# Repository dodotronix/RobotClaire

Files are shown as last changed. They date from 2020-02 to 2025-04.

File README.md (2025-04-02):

# ROBOT CLAIRE
This project is the result of three years of development from my high school
years. The main goal was to build my own robot from scratch, without using
common construction parts that are readily available in many hobbyist shops
today.

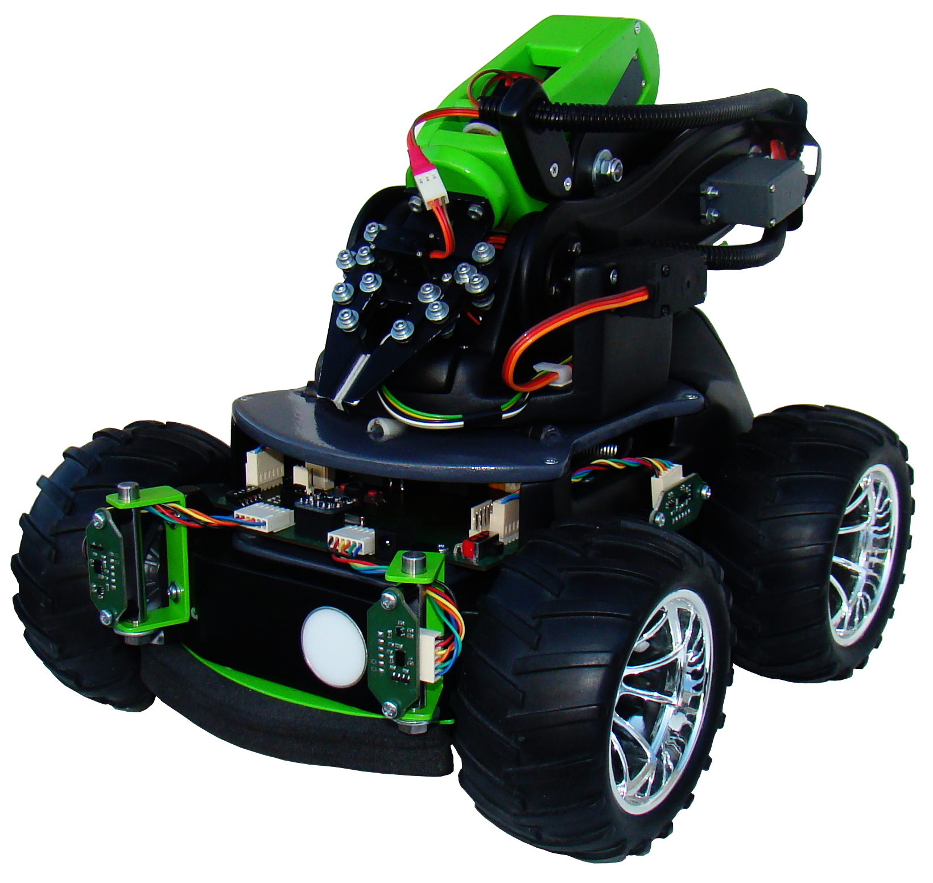
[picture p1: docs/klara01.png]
Robot

At the time when I was creating my robot, open-source CAD programs weren’t at a
sufficient level to design something that could be sent to a factory for
fabrication. For this reason, the mechanical design was created using Inventor
2013, while the electronic design was done using KiCad. The project has already
gone through three upgrades, but the first one wasn’t documented. However, I
did take some photos to capture the atmosphere of the very first steps in
development ([claire-rev0](https://drive.google.com/open?id=1PmOoYiifd_Xv0sS2DL9yxbEeKM7cLnv_)).

## NAVIGATION IN PROJECT
In the following folders, you will find README.md files with more detailed
descriptions of the content. Some folders also include additional information,
such as installation and execution instructions, particularly in directories
containing software. Please note that this repository is still under
development, and not all folders have been fully uploaded yet.

Video (http://www.youtube.com/watch?v=Z39dk2hXI14 "")

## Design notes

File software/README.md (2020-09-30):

# RASPBERRY PI application and diagram how it works

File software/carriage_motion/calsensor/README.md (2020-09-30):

# Calibration of IR triangulation sensors

## Analysis

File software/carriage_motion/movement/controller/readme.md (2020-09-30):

# PID controller design

## Analysis of input data
Data is read from the AddPU unit, which is sampling the number of ticks per
revolution of the motor shaft. Every motor has its ID (according to following
table) which is used to let the AddPU know, which data user want to read.

### Code identification
| Wheel | ID |
| :---: | :---: |
| right | 0xb0  |
| left  | 0xc0  |

### Wheel parameters measurement
| Parameter | Value [mm] |
| :---: | :---: |
| diameter | 118 |
|perimeter | 370.7 (calculated)|

### Wheel parameters measurement (comprises wheel deformation)
| Parameter | Value |
| :---: | :---: |
| revolutions |  3 |
| distance | 1086 [mm]  |
| ticks | 2935 |
| primeter | 362 [mm] |
| wheel gauge | 212 [mm] |

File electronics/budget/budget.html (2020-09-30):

obchod | koupě/prodej | počet | kód produktu | název produkutu | datum koupě/prodeje | cena produktu s DPH | poštovné | Cena + poštovné
HIMOTO | koupě | 2 | 08008CH08009 | HIMOTO MONSTER TRUCK KOLA 1:10 (2ks); | 11.10.2013 | 1180 | 100 | 3 860,-- Kč
| | | 1RC21105 | FOXY R-35B CAR BRUSHLESS ESC 35A | | 2580
RpiShop.cz | koupě | 1 | RPI_B_+ | Raspberry Pi Model B+ 512 MB RAM; | 31.12.2014 | 888 | 75 | 1 222,-- Kč
| | | SDHC_KINGST | Předinstalovaná 16GB Micro SDHC karta Kingston ON_16GB_MIC cl.10+Adaptér RO_ADA | | 259
SNAIL INSTRUMENTS | koupě | 1 | Ada 0757 | 4-channel I2C-safe Bi-directional Logic Level Converter | 30.12.2014 | 115 | 41 | 156,-- Kč
RpiShop.cz | koupě | 1 | RPI_B_RV2 | Sony Raspberry Pi Model B 512 MB RAM Rev. 2.0; | 09.12.2013 | 869 | 99 | 1 436,-- Kč
| | | RPI_CASE_PL_B | Raspberry Pi plastová krabička, case ČERNÁ | | 239
| | | LACK RPI_PWSP | Napájecí zdroj pro Raspberry Pi | | 229
SNAIL INSTRUMENTS | koupě | 1 | 000-000 | Sabertooth 2X5 | 04.11.2014 | 1490 | 41 | 1 531,-- Kč
SNAIL INSTRUMENTS | koupě | 4 | 208-001 | QRD1114; | 09.12.2013 | 96 | 88 | 4 788,-- Kč
| | 2 | 000-000 | Pololu1442; | | 2296
| | 1 | 000-000 | Sabertooth 2X5; | | 1490
| | | Pololu 1353 | Mini Maestro12 Kit | | 818
BIG HOBBY | koupě | 1 | B312b | BIG-power 2500 mah 3S 35C (70C); | 12.01.2015 | 672 | 100 | 1 137,-- Kč
| | | S010s1 | JX servo PDI-5521MG (digital) 55g/0,16sec/20kg | | 365
GME | koupě | 6 | ZBO 800-083 | MLWD6G | 14.11.2013 | 9.3 | - | 104,-- Kč
| | 9 | ZBO 840-002 | KONPC-SPK-2 | | 1.1
| | 9 | ZBO 840-003 | KONPC-SPK-3 | | 1.1
| | 50 | ZBO 840-004 | KONPC-SPK-PI | | 0.43
| | 4 | ZBO 840-005 | KONPC-SPK-4 | | 1.5
Jiří Kubín | koupě | 2 | - | 4cr-předplněný sprej | 12.09.2013 | 112.9 | - | 1 104,-- Kč
| | 1 | | Barva MI ř.700 11 | | 176.24
| | | | Debeer 4759 tužidlo 11 | | 77.24
| | | | MIPA barva BC | | 171.33
| | | | Mipa sprej lak 400ml | | 90.8
| | | | Profi primer šedý | | 157.3
| | | | Tmel na plasty 1kg | | 205.7
Jiří Kubín | koupě | 1 | - | Mipa sprej černý mat 400m | 06.01.2015 | 90.8 | - | 861,-- Kč
| | | | Mipa sprej lak 400ml | | 90.8
| | | | Mipa primer šedý | | 168.19
| | | | Mipa tmel na plasty P35 | | 220.22
| | | | Mipa brava BC 11 | | 178.23
| | | | Mipa předplněný sprej | | 113
Jiří Kubín | koupě | 1 | - | ředidlo C6000 700ml | 09.01.2015 | 55.8 | - | 224,-- Kč
| | | | Mipa primer šedý | | 168.19
RCKING HK | koupě | 1 | 1MA013 | Servo G0-13MG | 31.01.2014 | 170 | - | 170,-- Kč
GME | koupě | 2 | ZBO 650-062 | FBK10H | 14.11.2013 | 22.2 | - | 44,-- Kč
GME | koupě | 1 | ZBO 731-335 | N-EWZ225D | 14.11.2013 | 839 | - | 839,-- Kč
Zbyněk Pražák truhlářské potřeby & železářství | koupě | 1 | 92605 | kuličkový výsuv 10kg 17/406 | 22.03.2013 | 56 | - | 56,-- Kč
Drogerie Teta | koupě | 1 | - | Epoxyplast epox | 07.10.2013 | 79.9 | - | 100,-- Kč
| | | | Zapalovac domaci | | 19.9
GES | koupě | 1 | GES05303425 | Drátový potenciometr 4W zapouzdřený | 31.01.2014 | 99 | - | 99,-- Kč
GES | koupě | 1 | GES07203771 | Krabička dvoudílná plastová, 78x110x32mm, s úchyt, černá, plná | 12.03.2014 | 50 | - | 106,-- Kč
| | | GES07203753 | Krabička čtyřdílná plastová, 91x111x35mm, černá, plus vrut | | 56
SPOJOVACI A UPEVNOVACI MATERIALY - NOVOTNY | koupě | 10 | - | SR PLECH 2.9x19 ZH DIN 7982 | 20.01.2015 | 0.25 | - | 22,-- Kč
| | 12 | | Cervik plochy M4x5 DIN 913 | | 1
| | 8 | | Cervik plochy M3x5 DIN 913 | | 0.9
GME | koupě | 10 | ZBO 980-001 | CK1210 10M/25V Y5VSM | 5.11.2014 | 7.13 | - | 201,-- Kč
| | 3 | ZBO 523-265 | QRD1114 | | 25.76
| | 10 | ZBO 905-081 | CK1206 100N/50VK7R | | 0.8
| | 1 | ZBO 634-714 | RELAUTO12V-30A | | 44
GME | koupě | 50 | ZBO 840-004 | KONPC-SPK-PI | 23.12.2014 | 0.48 | - | 61,-- Kč
| | 1 | ZBO 746-001 | S-FIX PLS0.3 | | 29.12
| | 1 | ZBO 611-013 | TL.10uH | | 8.32
GME | koupě | 2 | ZBO 511-434 | LED 5MM PURE GREEN | 12.03.2014 | 11.65 | - | 49,-- Kč
| | | ZBO 511-315 | LED 5MM YELLOW 80C | | 5.6
| | | ZBO 511-607 | LED 5MM RED 8000/20 | | 7.39
GME | koupě | - | - | - | 12.04.2014 | - | - | 76,-- Kč
IZOSTAV | koupě | 1 | - | Barva sprej 400ml | 02.10.2013 | 93 | - | 93,-- Kč
GME | koupě | - | - | - | 12.04.2014 | - | - | 150,-- Kč
SPOJOVACI A UPEVNOVACI MATERIALY – NOVOTNY | koupě | 30 | - | Kruh.podlozka 6x12 0.1 mm | 30.10.2013 | 1 | - | 108,-- Kč
| | | | Kruh.podlozka 6x12 0.2 mm
| | 20 | | PODL tezka 6.4 BP DIN 7349 | | 1.2
| | | | PODL 6.0 pro kolik ZN ISO 8738
SPOJOVACI A UPEVNOVACI MATERIALY – NOVOTNY | koupě | 5 | - | POJ KROUZ.TRMEN 5 mm BP D.6799 | 07.10.2013 | 0.5 | - | 43,-- Kč
| | 20 | | SR PLECH 2.9x19 ZH DIN 7982 | | 0.25
| | 4 | | Cervik plochy M3x3 BP DIN 913 | | 0.8
| | 1 | | Klic imbus 1.5 Balldr.karta | | 0.28
| | 10 | | PODL 4.3 ZN DIN 125 | | 0.08
| | | | MAT POJ M3 ZN DIN 985 | | 0.35
GME | koupě | 4 | ZBO 800-098 | PSH02-04W | 23.12.2014 | 2.2 | - | 89,-- Kč
| | | ZBO 800-039 | PSH02-06B BEZOVA | | 2.8
| | | ZBO 800-088 | PFH02-06P | | 2.13
| | | ZBO 800-086 | PFH02-04P | | 1.79
| | 24 | ZBO 800-112 | PFF02-04P | | 1.12
| | 3 | ZBO 651-195 | RG-MD122-BAL | | 7.06
| | 1 | ZBO 824-018 | SIL05PZ | | 5.6
GME | koupě | 3 | ZBO 650-062 | FBK10H | 12.04.2014 | 24.86 | - | 150,-- Kč
| | 10 | ZBO 800-085 | PFH02-03P | | 1.23
| | | ZBO 800-163 | PSH02-02PG
| | 5 | ZBO 840-003 | KONPC-SPK-3
| | 30 | ZBO 800-112 | PFF02-01F | | 1.01
| | 20 | ZBO 840-004 | KONPC-SPK-PI | | 0.56
| | 1 | ZBO 114-044 | RR W2 E022 | | 3.36
Š-HOBBY HK | koupě | 1 | - | LM3940IT-3.3V/1A LDO TO220 stab. | 31.01.2014 | 38 | - | 62,-- Kč
| | | | 7805 TO220 nap.stap.+5V/1A /STM | | 7.5
| | | | 1N53428 ZENER.DIODA 6.8V 5W | | 9.5
| | 2 | | ZD6V8 1.3W | | 2
| | | | ZD7V5 1.3W | | 1.5
GES | koupě | 6 | GES06614038 | BLS 03 | 25.10.2013 | 0.83 | - | 119,-- Kč
| | 18 | GES06614047 | BLS CONTACTS | | 0.44
| | 3 | GES06914175 | SPP 4 | | 5.62
| | | GES06614438 | WSL 10W | | 2.73
| | | GES06614738 | PFL 10 | | 3.55
| | 2 | GES06900229 | AWG 28-10G | | 9.09
| | | GES07203782 | KP 32 | | 15.7
GME | koupě | 5 | ZBO 210-018 | BC337-25 | 23.12.2014 | 1.25 | - | 393,-- Kč
| | 5 | ZBO 210-023 | BC546A | | 1.23
| | 2 | ZBO 824-025 | DIL28PZ 7,5mm | | 18.03
| | 1 | ZBO 432-201 | Atmega8-16PU | | 94
| | 10 | ZBO 110-049 | RR 100R | | 2.24
| | 10 | ZBO 110-053 | RR 150R | | 2.24
| | 10 | ZBO 110-055 | RR 180R | | 2.24
| | 10 | ZBO 110-056 | RR 200R | | 2.24
| | 1 | ZBO 131-075 | QM 16.000MHZ | | 10.08
| | 2 | ZBO 120-105 | CK 100N/50V2 X7R | | 2.8
| | 2 | ZBO 120-125 | CKS 22P/50V | | 2.24
| | 1 | ZBO 611-066 | 09P-103J | | 13
| | 2 | ZBO 800-171 | PSH02-04WG | | 2.8
| | 2 | ZBO 800-173 | PSH02-06WG | | 3.7
| | 2 | ZBO 800-088 | PFH02-06P | | 2.13
| | 2 | ZBO 800-086 | PFH02-04P | | 1.79
| | 20 | ZBO 800-112 | PFF02-01F | | 1.12
| | 2 | ZBO 511-359 | L-937EGW | | 4
| | 2 | ZBO 511-561 | LED 3MM BLUE 3500/2 | | 8
| | 1 | ZBO 511-681 | LED 3MM RED 4000/30 | | 3.3
| | 1 | ZBO 511-533 | LED 3MM YELLOW 500 | | 4
| | 2 | ZBO 523-265 | QRD1114 | | 25.76
| | 1 | ZBO 210-030 | BC548C | | 0.89
| | 1 | ZBO 215-003 | 2N3904 | | 0.85
| | 534 | | | | | | 19 846,-- Kč

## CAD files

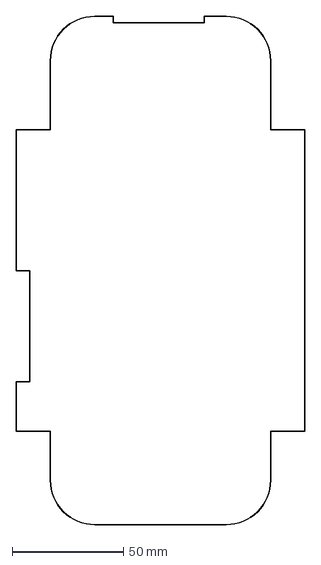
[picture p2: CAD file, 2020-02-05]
mechanics/CAD_design/Robot_Klara/test1.dxf
130.0 x 229.0 mm

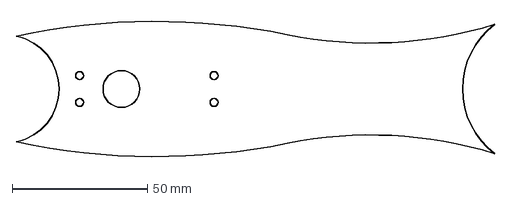
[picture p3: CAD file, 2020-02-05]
mechanics/CAD_design/robotic arm/rameno/na_vyfrezovani/k odeslani/k vyfrezovani/7mm-komatex-1clanek(B2)(1x).dxf
176.8 x 53.6 mm

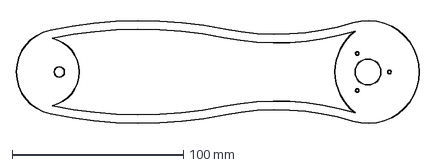
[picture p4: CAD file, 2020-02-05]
mechanics/CAD_design/robotic arm/rameno/na_vyfrezovani/k odeslani/sablona_2.dxf
236.9 x 64.9 mm

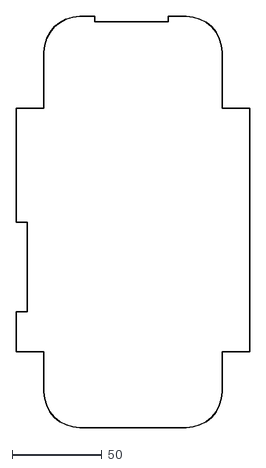
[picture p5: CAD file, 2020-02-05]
mechanics/CAD_design/Robot_Klara/test.dxf
130.0 x 229.0

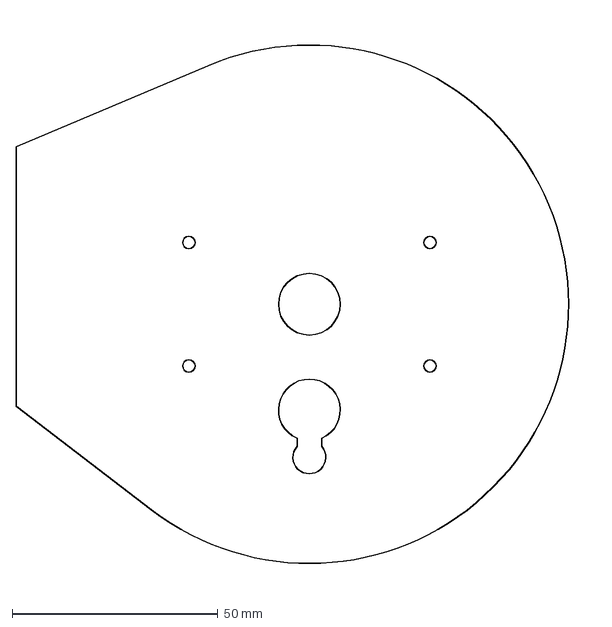
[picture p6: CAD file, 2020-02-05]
mechanics/CAD_design/robotic arm/rameno/na_vyfrezovani/k odeslani/k vyfrezovani/4mm-komatex-otocny-kruh(1x).dxf
140.8 x 138.6 mm

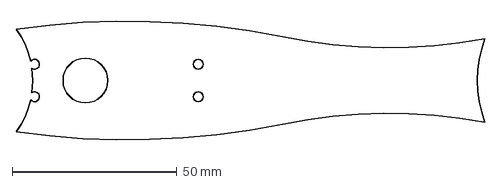
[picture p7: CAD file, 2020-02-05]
mechanics/CAD_design/robotic arm/rameno/na_vyfrezovani/k odeslani/sablona_1.dxf
142.4 x 38.9 mm

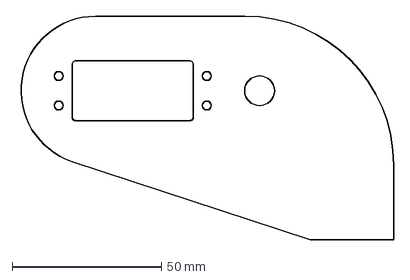
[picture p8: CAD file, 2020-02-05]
mechanics/CAD_design/robotic arm/rameno/na_vyfrezovani/k odeslani/k vyfrezovani/3mm-komatex_clanek3(B1)(1x).dxf
126.6 x 75.0 mm

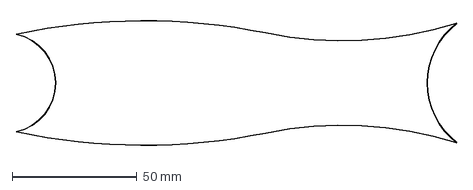
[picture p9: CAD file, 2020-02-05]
mechanics/CAD_design/robotic arm/rameno/na_vyfrezovani/k odeslani/k vyfrezovani/7mm-komatex-1clanek(A2)(1x).dxf
176.8 x 53.6 mm

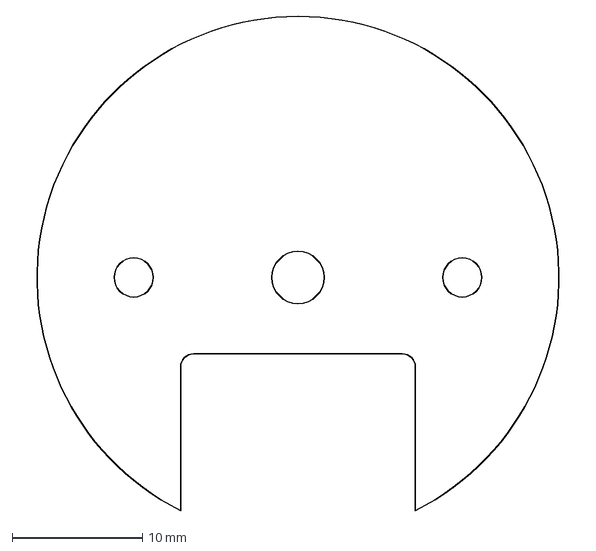
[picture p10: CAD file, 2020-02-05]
mechanics/CAD_design/robotic arm/rameno/na_vyfrezovani/k odeslani/k vyfrezovani/10mm-komatex-profil-packa(1x).dxf
43.2 x 37.9 mm

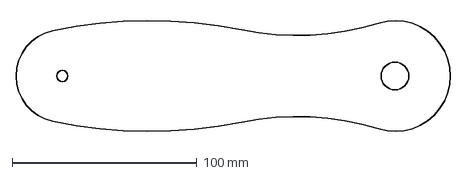
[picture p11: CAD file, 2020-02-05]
mechanics/CAD_design/robotic arm/rameno/na_vyfrezovani/k odeslani/k vyfrezovani/5mm-komatex-1clanek(A1)(1x).dxf
236.9 x 64.9 mm

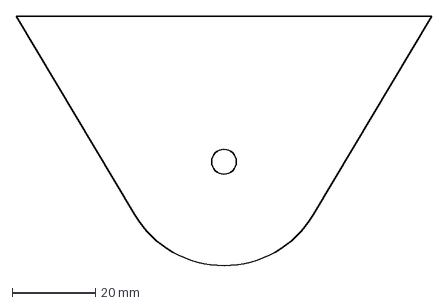
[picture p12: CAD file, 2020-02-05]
mechanics/CAD_design/robotic arm/rameno/na_vyfrezovani/k odeslani/k vyfrezovani/10mm-komatex-profil-stojan(2x).dxf
100.0 x 60.0 mm

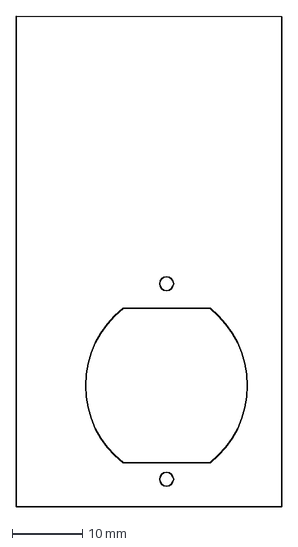
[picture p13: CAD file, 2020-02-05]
mechanics/CAD_design/robotic arm/rameno/na_vyfrezovani/k odeslani/k vyfrezovani/5mm-komatex_uchyceni_micro-serva(1x).dxf
37.9 x 70.0 mm

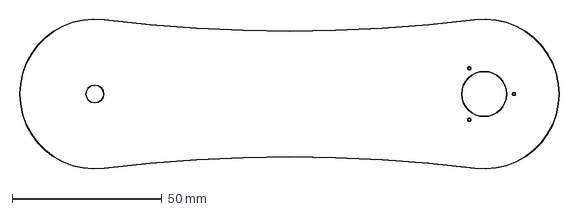
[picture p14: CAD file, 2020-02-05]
mechanics/CAD_design/robotic arm/rameno/na_vyfrezovani/k odeslani/k vyfrezovani/5mm-komatex-2clanek(A)(1x).dxf
182.6 x 52.0 mm

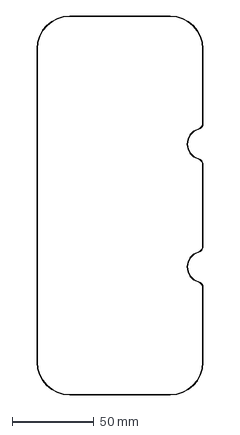
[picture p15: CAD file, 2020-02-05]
mechanics/CAD_design/robotic arm/rameno/na_vyfrezovani/k odeslani/k vyfrezovani/podvozek_horni_kryt(2).dxf
101.2 x 231.3 mm

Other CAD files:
mechanics/CAD_design/robotic arm/rameno/na_vyfrezovani/k odeslani/k vyfrezovani/5mm-komatex-1clanek(B1)(1x).dxf
mechanics/CAD_design/robotic arm/rameno/na_vyfrezovani/k odeslani/k vyfrezovani/5mm-komatex-2clanek(B)(1x).dxf
mechanics/CAD_design/robotic arm/rameno/na_vyfrezovani/k odeslani/k vyfrezovani/3mm-komatex-desticka_na_lozisko(8x).dxf
mechanics/CAD_design/robotic arm/rameno/na_vyfrezovani/k odeslani/k vyfrezovani/4mm-komatex_clanek3(B2)(1x).dxf
mechanics/CAD_design/Robot_Klara/DC_motor+enkoder.ipt
mechanics/CAD_design/Robot_Klara/Lozisko_15mm.ipt
mechanics/CAD_design/Robot_Klara/OldVersions/DC_motor+enkoder.0004.ipt
mechanics/CAD_design/Robot_Klara/OldVersions/Lozisko_15mm.0001.ipt
mechanics/CAD_design/Robot_Klara/OldVersions/PCB_kon_drzak.0003.ipt
mechanics/CAD_design/Robot_Klara/OldVersions/Robot_Klara.0072.iam
mechanics/CAD_design/Robot_Klara/OldVersions/Robot_Klara.0079.iam
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

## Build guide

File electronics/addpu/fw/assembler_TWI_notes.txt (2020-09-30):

po porohozeni vetvi zjisteny jednotlive navesti:

0xC0 ---- .L10
0xC8 ---- .L11
0xA8 ---- .L12
0xA0 ---- .L5
0x88 ---- .L13; .L8
0x60 ---- .L7
0x00 ---- .L9 (pri spravne pozici CASEu  muze byt zrusena)

z datasheetu:
0x36 == TWCR
0x1 tzn. 0x01 ---- TWSR
0x3 tzn. 0x03 ---- TWDR

- hodnoty jsou napsane v decimalce
- minusove hodnoty musi byt odecteny od cisla 256, pro ziskani zakodovaneho cisla

vymaskovani ---- (-8) tzn 0xF8

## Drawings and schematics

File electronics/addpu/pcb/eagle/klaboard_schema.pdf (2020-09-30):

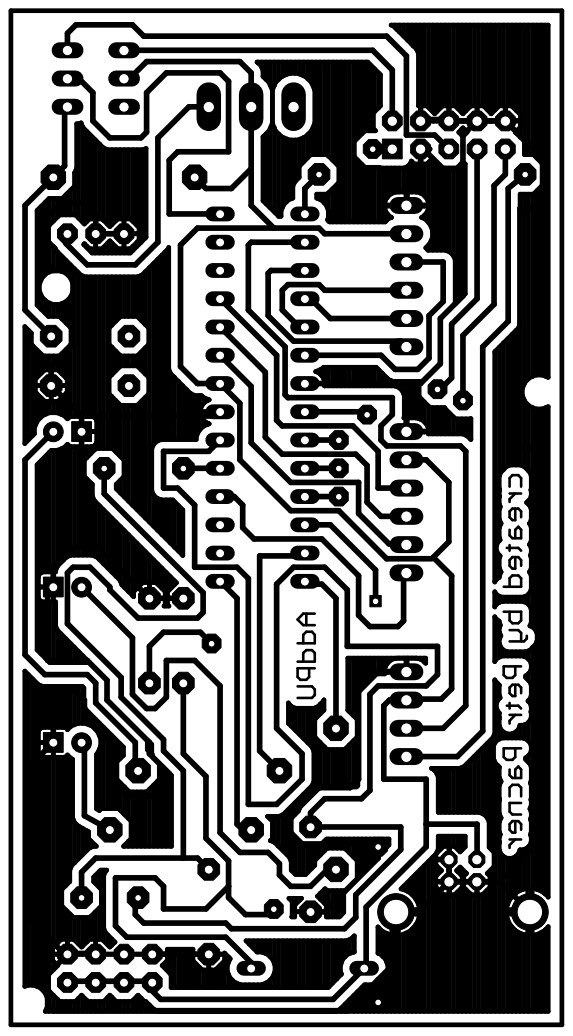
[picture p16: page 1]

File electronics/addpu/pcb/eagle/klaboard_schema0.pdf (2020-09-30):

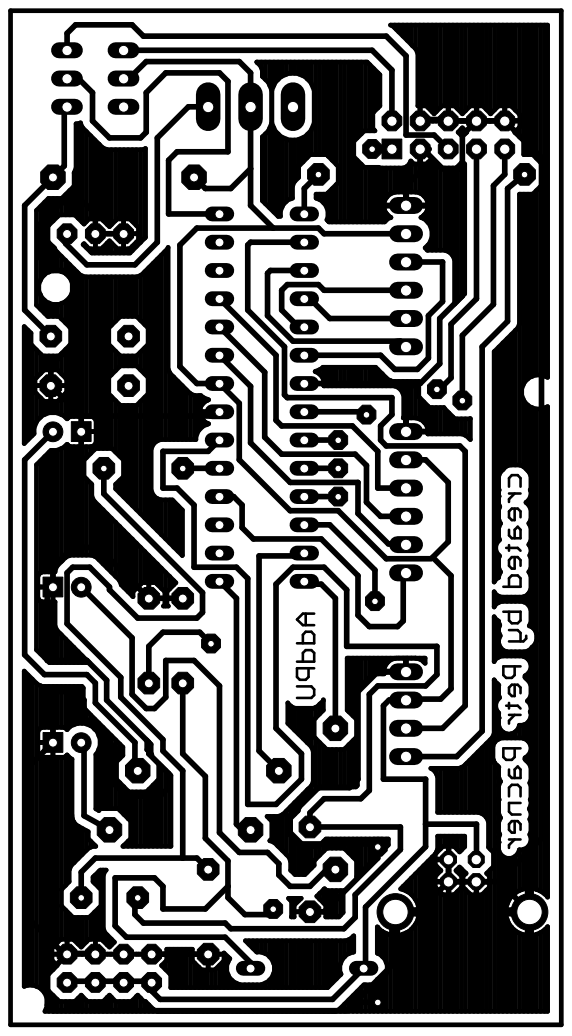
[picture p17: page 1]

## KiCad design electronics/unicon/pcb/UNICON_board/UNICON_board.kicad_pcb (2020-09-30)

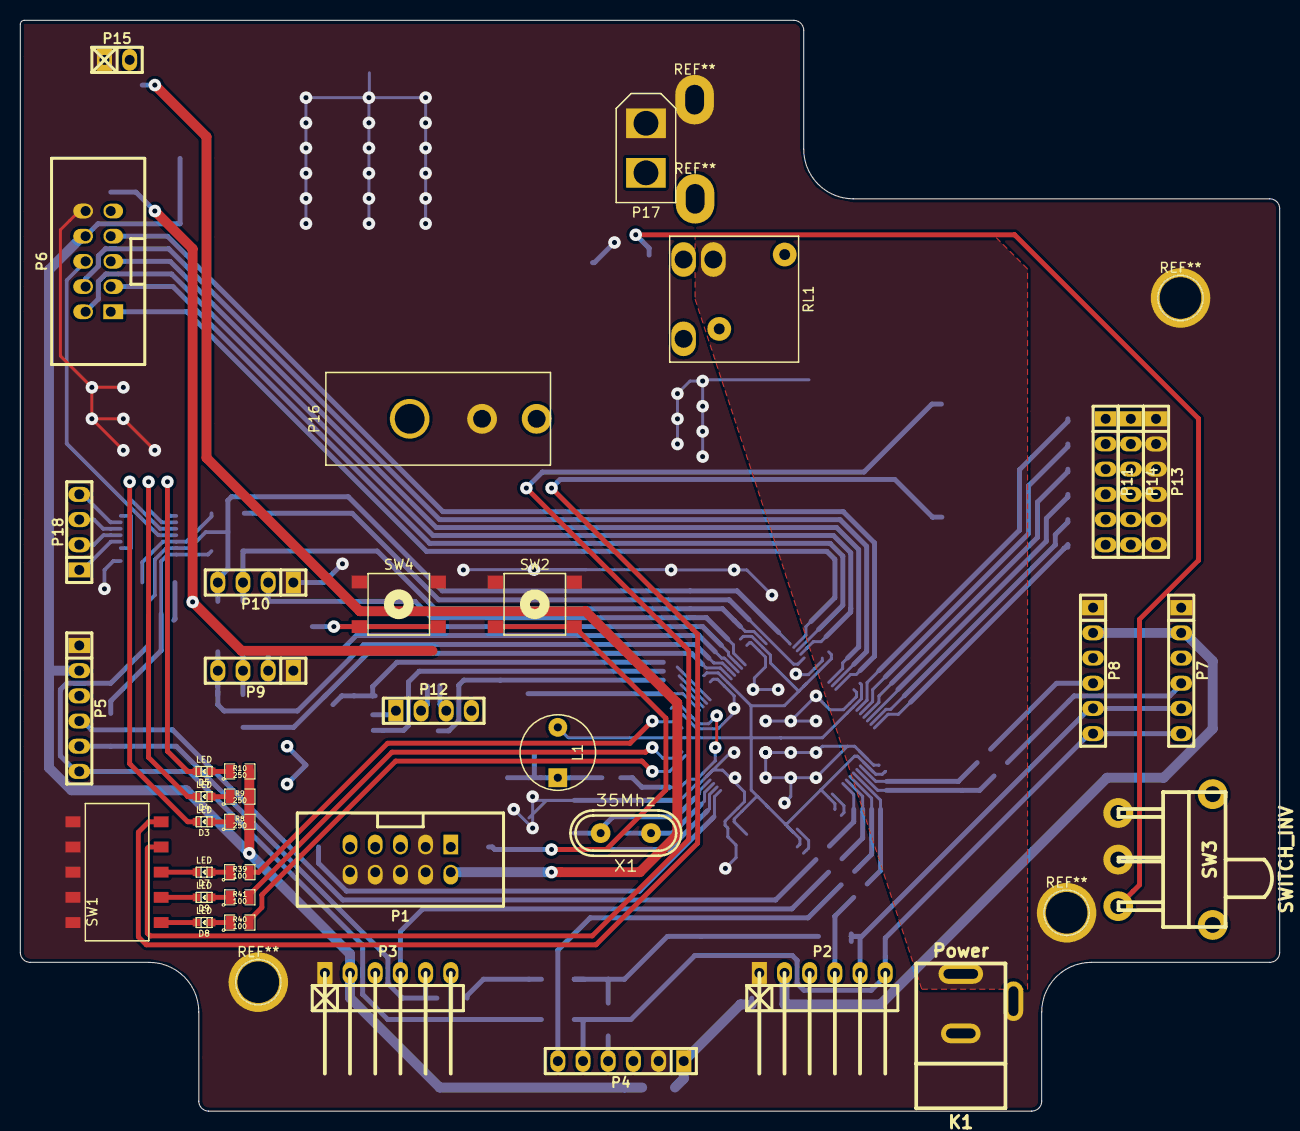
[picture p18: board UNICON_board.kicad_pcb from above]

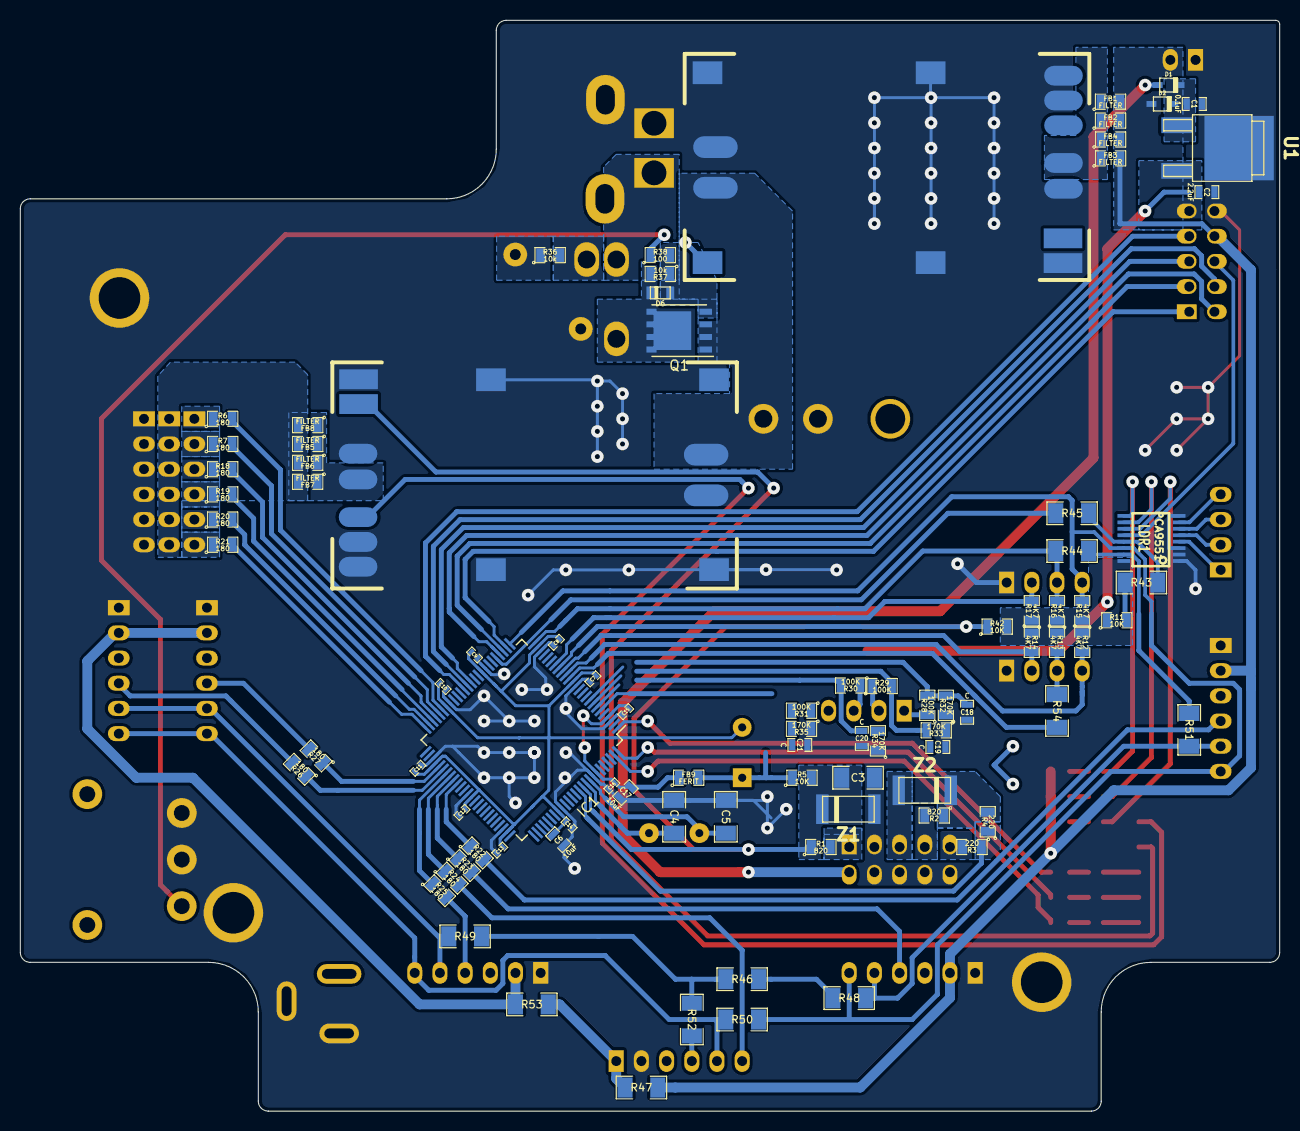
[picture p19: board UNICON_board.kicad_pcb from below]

Board: 2 copper layers, 127.0 x 110.0 mm, 127 parts (89 on the bottom side), 106 nets.

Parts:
C1: 0.1uF; SM0603_Capa
C2: 2.2uF; SM0603_Capa
C3, C4, C5: 22pF; SM1206
C6, C17: 10uF; SM0603_Capa
C7, C8, C9, C10, C11, C12, C13, C14, C15, C16: 100nF; SM0402
C18, C19, C20, C21: C; SM0603_Capa
D1, D2: DIODESCH; sod323
D3, D4, D5, D7, D8, D9: LED; Led_0603
D6: ZENER; micromelf
FB1, FB2, FB3, FB4, FB5, FB6, FB7, FB8: FILTER; SM0805
FB9: FERIT; SM0805
IC1: ATXMEGA64A1-A; TQFP-100_14x14mm_Pitch0.5mm
K1: Power; dc_socket
L1: 10uH; INDUCTOR_V
LDR1: PCA9551; TSSOP16
P1: CONN_5X2; vasch_strip_5x2
P2: Sens3; pin_strip_6-90
P3: Sens2; pin_strip_6-90
P4: compss; pin_socket_6
P5: Sens4; pin_strip_6
P6: Supp_board; vasch_strip_5x2
P7: Sens0; pin_strip_6
P8: Sens1; pin_strip_6
P9: I2C_1; pin_strip_4
P10: I2C_0; pin_strip_4
P11, P13, P14: CONN_6; pin_strip_6
P12: CONN_4; pin_strip_4
P15: RPI_supp; pin_strip_2
P16: Add_BRD; MOLEX_mega_fit_2
P17: BATT; XT30
P18: GPIOs; pin_strip_4
Q1: BS133; SO-8_PowerPAK_Vishay
R1, R2: 820; SM0805
R3, R4: 220; SM0805
R5, R11, R42: 10K; SM0805
R6, R7, R18, R19, R20, R21, R22, R23, R24, R25, R26, R27: 180; SM0805
R8, R9, R10: 250; SM0805
R12, R13, R14, R15, R16, R17: 4K7; SM0805
R28, R29, R30, R31: 100K; SM0805
R32, R33, R34, R35: 170K; SM0805
R36, R37: 10k; SM0805
R38, R39, R40, R41: 100; SM0805
R43, R44, R46, R47, R48, R49, R50, R51, R52, R53, R54: 0; SM1206
R45: 180; SM1206
RL1: relay; relay_TRS_L_12
S1, S2: UBEC(5A); UBEC_5A
SW1: DIPS_05; dip_switch_5
SW2: REBOOT; Button_smd
SW3: SWITCH_INV; switch_mfp116dg-ra
SW4: MODE; Button_smd
U1: LF33CDT; d-pak
X1: 35Mhz; crystal_hc-49s
Z1, Z2: 3V6; melf

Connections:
5Vin: D1.1, P1.2
5Vout: D2.1, FB1.2, FB2.2, FB3.2, FB4.2, P3.2, P5.2, P6.8, P15.2, R8.2, R9.2, R10.2, R47.1
+3v3: C2.1, FB9.2, L1.1, LDR1.16, P6.9, R5.1, R11.1, R12.1, R13.1, R14.1, R15.1, R16.1, R17.1, R42.2, U1.3
+6Vout: FB5.2, FB6.2, FB7.2, FB8.2, P14.1, P14.2, P14.3, P14.4, P14.5, P14.6
+12V: P16.2, Q1.1, S1.1, S2.1
ADC_0: C21.1, IC1.6, R31.2, R35.2
ADC_1: C20.1, IC1.7, R30.2, R34.2
ADC_2: C19.1, IC1.8, R29.2, R33.2
ADC_3: C18.1, IC1.9, R28.2, R32.2
CLK_PDI: C3.1, IC1.90, R1.1, R5.2, SW2.1, Z1.2
DT_PDI: IC1.89, R3.1, R4.1
GND: C1.2, C2.2, C3.2, C4.2, C5.2, C6.1, C7.1, C8.1, C9.1, C10.1, C11.1, C12.1, C13.1, C14.1, C15.1, C16.1, C17.1, C18.2, C19.2, C20.2, C21.2, IC1.3, IC1.13, IC1.23, IC1.33, IC1.43, IC1.53, IC1.63, IC1.73, IC1.84, IC1.93, K1.1, K1.2, LDR1.1, LDR1.2, LDR1.3, LDR1.8, P1.3, P1.4, P1.6, P1.8, P1.10, P2.1, P3.1, P4.2, P5.1, P6.10, P7.1, P8.1, P9.1, P10.1, P13.1, P13.2, P13.3, P13.4, P13.5, P13.6, P15.1, P16.1, P17.1, R32.1, R33.1, R34.1, R35.1, RL1.5, S1.5, S2.5, SW1.1, SW1.2, SW1.3, SW1.4, SW1.5, SW2.2, SW3.2, SW3.3, SW4.2, U1.2, Z1.1
I2C_0+: LDR1.15, R44.2, R51.1
I2C_0-: IC1.26, LDR1.14, P3.6, P5.6, P10.4, R15.2, R50.1
I2C_1+: IC1.15, R54.1
I2C_1-: IC1.16, P9.4, R12.2
INT_0: IC1.19, P10.2, R17.2
INT_1: IC1.17, P9.2, R14.2
INT_A_0: IC1.28, P6.3
INT_A_1: IC1.39, P6.7
INT_B_0: IC1.27, P6.1
INT_B_1: IC1.37, P6.5
Light: LDR1.12, P6.6
MTR_0: IC1.29, P6.2
MTR_1: IC1.38, P6.4
unnamed: C1.1, D1.2, D2.2, U1.1
unnamed: C4.1, IC1.91, X1.1
unnamed: C5.1, IC1.92, X1.2
unnamed: C6.2, C7.2, C8.2, C9.2, C10.2, C11.2, C12.2, C13.2, C14.2, IC1.14, IC1.24, IC1.34, IC1.44, IC1.54, IC1.64, IC1.74, IC1.83, L1.2
unnamed: C15.2, C16.2, C17.2, FB9.1, IC1.4, IC1.94
unnamed: D3.1, R8.1
unnamed: D3.2, LDR1.11
unnamed: D4.1, R9.1
unnamed: D4.2, LDR1.10
unnamed: D5.1, R10.1
unnamed: D5.2, LDR1.9
unnamed: D6.1, Q1.2, R37.1, R38.2
unnamed: D6.2, Q1.3, R37.2, RL1.3
unnamed: D7.1, R39.1
unnamed: D8.1, R40.1
unnamed: D9.1, R41.1
unnamed: FB1.1, FB2.1, FB3.1, FB4.1, S1.2
unnamed: FB5.1, FB6.1, FB7.1, FB8.1, S2.2
unnamed: IC1.1, R39.2
unnamed: IC1.18, R42.1, SW4.1
unnamed: IC1.25, P10.3, R16.2, R44.1
unnamed: IC1.30, R45.2
unnamed: IC1.45, R6.2
unnamed: IC1.46, R7.2
unnamed: IC1.47, R18.2
unnamed: IC1.48, R19.2
unnamed: IC1.49, R20.2
unnamed: IC1.50, R21.2
unnamed: IC1.55, R27.1
unnamed: IC1.56, R26.1
unnamed: IC1.57, R25.1
unnamed: IC1.58, R24.1
unnamed: IC1.59, R23.1
unnamed: IC1.60, R22.1
unnamed: IC1.99, R40.2
unnamed: IC1.100, R41.2
unnamed: K1.3, R36.2, RL1.2
unnamed: LDR1.4, P18.1
unnamed: LDR1.5, P18.2
unnamed: LDR1.6, P18.3
unnamed: LDR1.7, P18.4
unnamed: P1.1, R1.2
unnamed: P1.5, Z2.1
unnamed: P1.7, R2.2
unnamed: P1.9, R3.2
unnamed: P2.2, P7.2, P8.2, R53.2
unnamed: P2.5, P7.5, P8.5, R49.2
unnamed: P2.6, P4.5, P7.6, P8.6, R50.2
unnamed: P3.5, P5.5, R48.1, R51.2
unnamed: P4.1, R47.2, R53.1
unnamed: P4.4, R52.1
unnamed: P9.3, R13.2, R54.2
unnamed: P11.1, R6.1
unnamed: P11.2, R7.1
unnamed: P11.3, R18.1
unnamed: P11.4, R19.1
unnamed: P11.5, R20.1
unnamed: P11.6, R21.1
unnamed: P12.1, R28.1
unnamed: P12.2, R29.1
unnamed: P12.3, R30.1
unnamed: P12.4, R31.1
unnamed: P17.2, RL1.1
unnamed: R2.1, R4.2, Z2.2
unnamed: R11.2, R43.2
unnamed: R36.1, RL1.4
unnamed: R46.1, R48.2
unnamed: R46.2, R49.1, R52.2
ON/OFF: R38.1, SW3.1
RST: LDR1.13, R43.1, R45.1
SW0: S2.3, SW1.10
SW1: S2.4, SW1.9
SW2: D9.2, SW1.7
SW3: D8.2, SW1.6
SW4: D7.2, SW1.8
sens0int: P7.4, R26.2
sens1int: P8.4, R27.2
sens2int: P3.4, R23.2
sens3int: P2.4, R25.2
sens4int: P5.4, R22.2
speed_up: P4.6, R24.2

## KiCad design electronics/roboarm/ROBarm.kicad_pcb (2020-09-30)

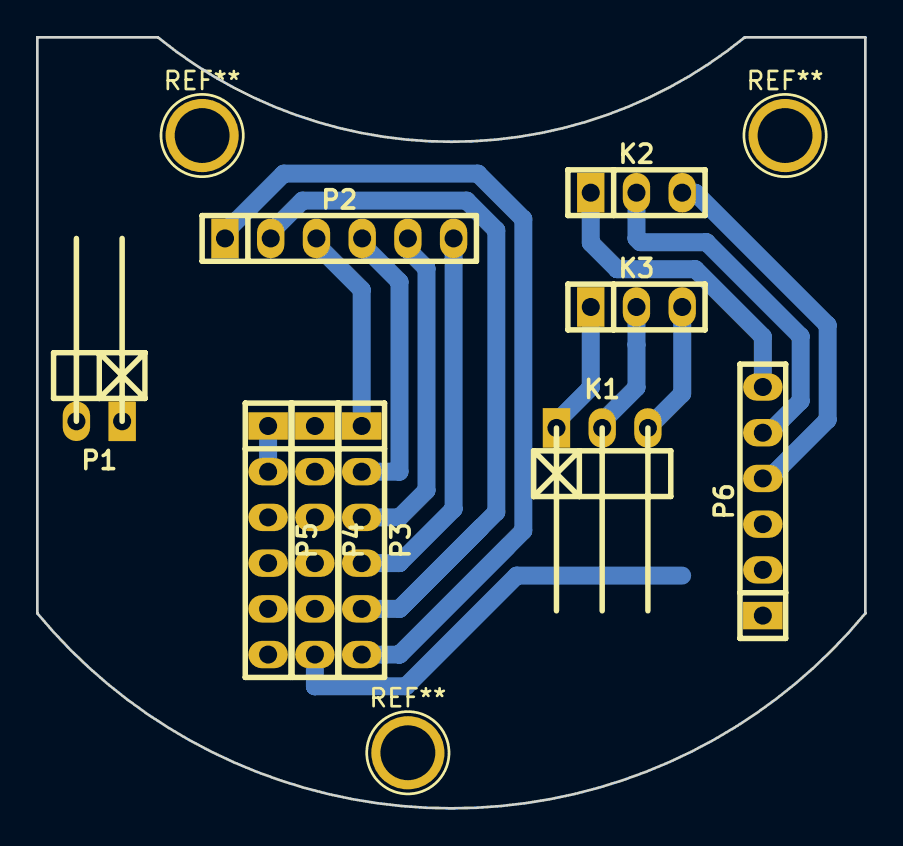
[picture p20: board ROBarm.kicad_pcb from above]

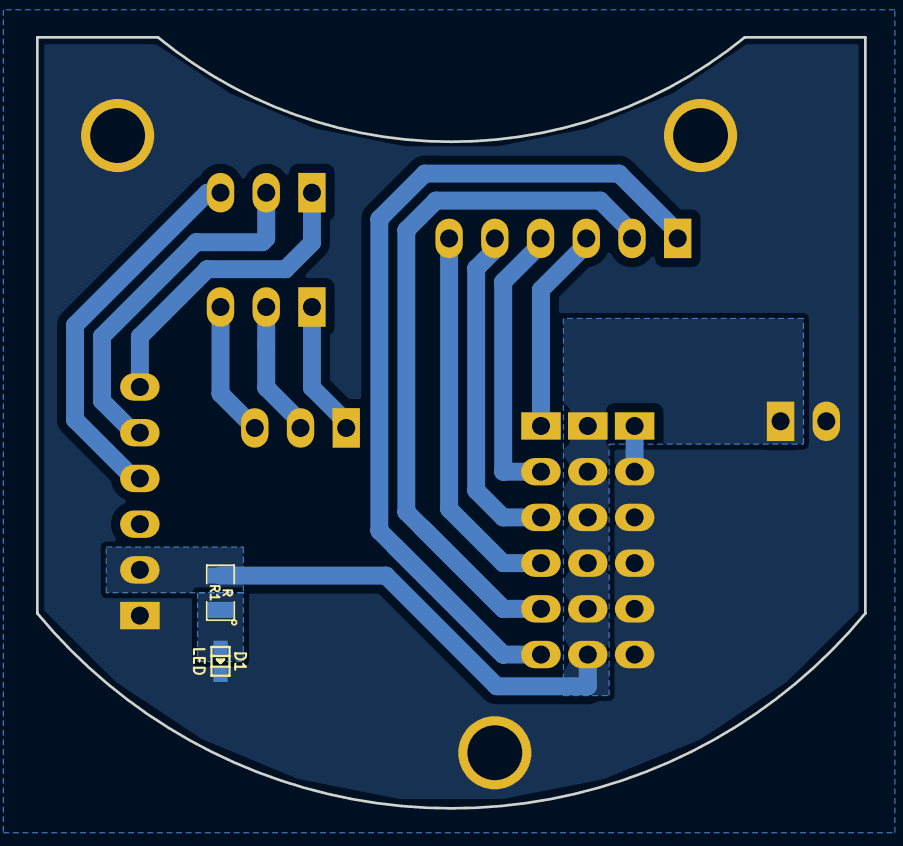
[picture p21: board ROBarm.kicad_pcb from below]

Board: 2 copper layers, 46.0 x 42.8 mm, 11 parts (2 on the bottom side), 15 nets.

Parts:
D1: LED; Led_0603
K1: CONN_3; pin_strip_3-90
K2, K3: CONN_3; pin_strip_3
P1: CONN_2; pin_strip_2-90
P2, P3, P4, P5, P6: CONN_6; pin_strip_6
R1: R; SM0805

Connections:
+6V: P1.1, P4.1, P4.2, P4.3, P4.4, P4.5, P4.6, P6.2, R1.2
GND: D1.2, P1.2, P5.1, P5.2, P5.3, P5.4, P5.5, P5.6, P6.1
IO_0: K2.3, P6.4
unnamed: D1.1, R1.1
PTCM+: K1.2, K3.2
PTCM-: K1.1, K3.1
PTCMs: K1.3, K3.3
SCL: K2.1, P6.6
SDA: K2.2, P6.5
SRV_0: P2.3, P3.1
SRV_1: P2.4, P3.2
SRV_2: P2.5, P3.3
SRV_3: P2.6, P3.4
SRV_4: P2.2, P3.5
SRV_5: P2.1, P3.6

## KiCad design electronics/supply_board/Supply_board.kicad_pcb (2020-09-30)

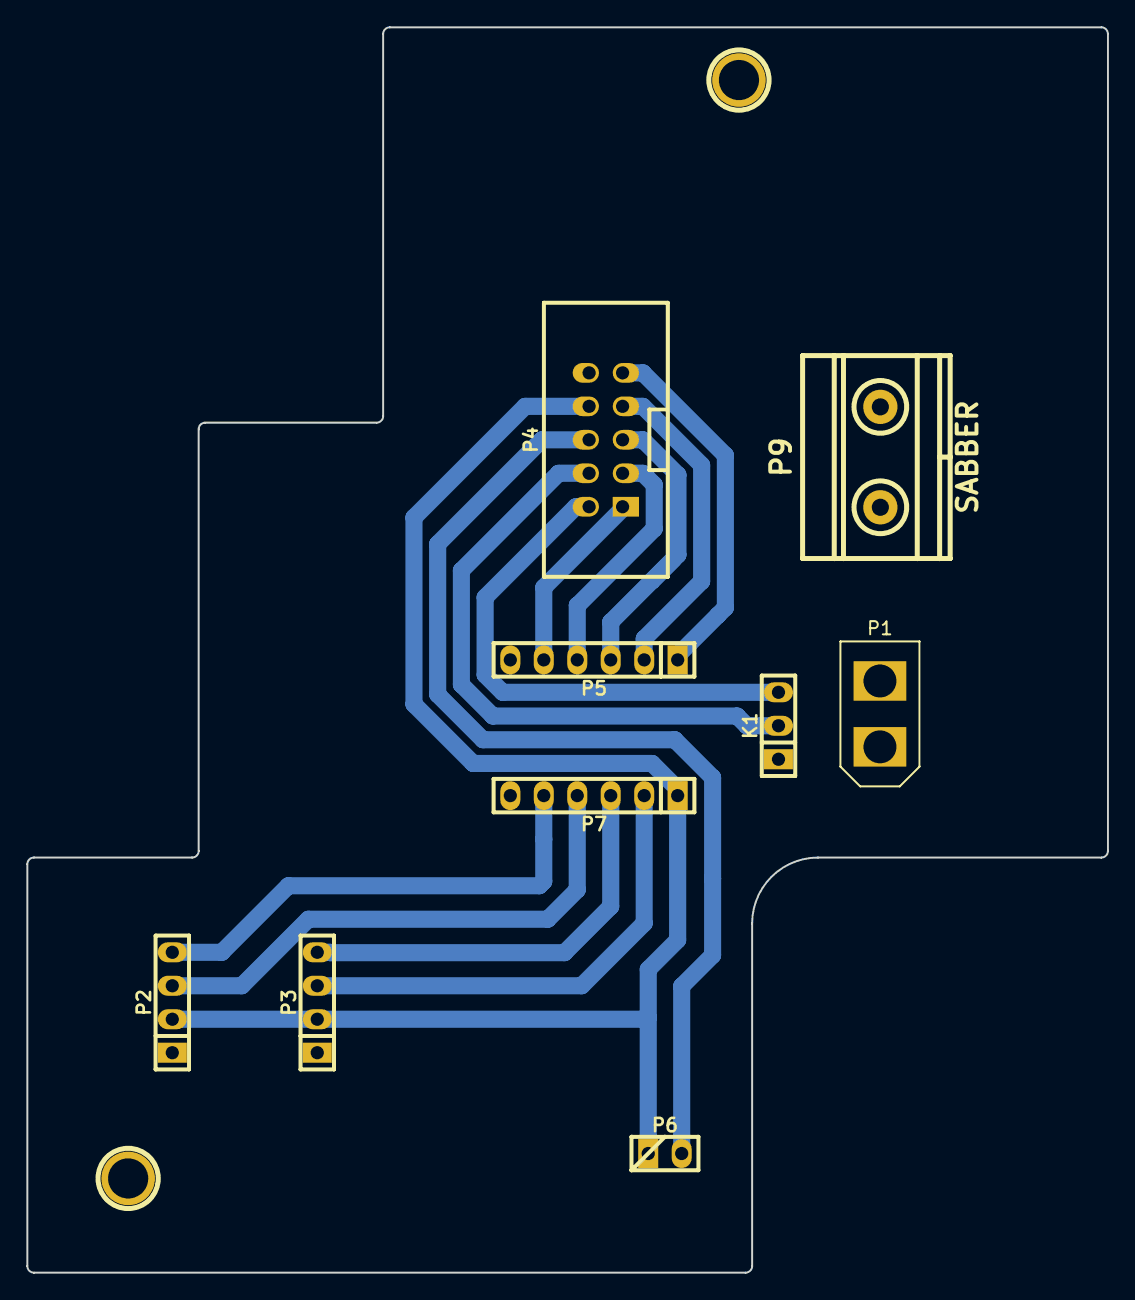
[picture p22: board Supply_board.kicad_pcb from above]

Board: 2 copper layers, 82.0 x 94.5 mm, 11 parts (0 on the bottom side), 15 nets.

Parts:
1PIN, 2PIN: P***; 1pin
K1: SIG_MTR; pin_strip_3
P1: BATT; XT30
P2: ENK0; pin_strip_4
P3: ENK1; pin_strip_4
P4: SIGNALS; vasch_strip_5x2
P5, P7: LV_SHIFT; pin_socket_6
P6: LED_SIG; pin_strip_2
P9: SABBER; gmkds_3-2-7,62

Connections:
+3V3: P4.9, P5.1
+5V: P2.2, P3.2, P4.8, P6.1, P7.1
+12V: P1.2, P9.1
ENC_A_0: P2.3, P7.4
ENC_A_1: P3.3, P7.2
ENC_B_0: P2.4, P7.5
ENC_B_1: P3.4, P7.3
GND: 1PIN.2, 2PIN.1, K1.1, P1.1, P2.1, P3.1, P4.10, P5.6, P7.6, P9.2
INT_A_0: P4.3, P5.4
INT_A_1: P4.7, P5.2
INT_B_0: P4.1, P5.5
INT_B_1: P4.5, P5.3
LED: P4.6, P6.2
MTR_0: K1.3, P4.2
MTR_1: K1.2, P4.4

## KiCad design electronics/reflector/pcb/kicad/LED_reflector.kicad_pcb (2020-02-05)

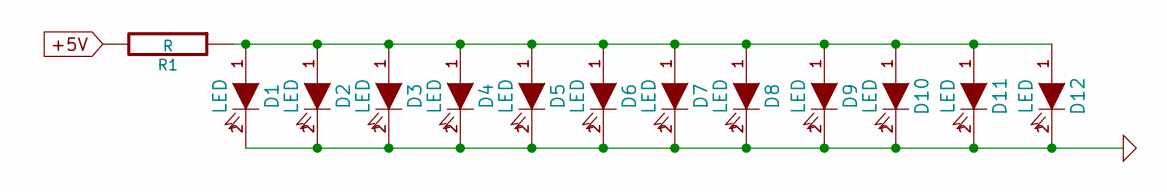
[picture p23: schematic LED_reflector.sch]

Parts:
D1, D2, D3, D4, D5, D6, D7, D8, D9, D10, D11, D12: LED; Led_0603
R1: R; SM0805

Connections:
+5V: R1.2
GND: D1.2 (K), D2.2 (K), D3.2 (K), D4.2 (K), D5.2 (K), D6.2 (K), D7.2 (K), D8.2 (K), D9.2 (K), D10.2 (K), D11.2 (K), D12.2 (K)
unnamed: D1.1 (A), D2.1 (A), D3.1 (A), D4.1 (A), D5.1 (A), D6.1 (A), D7.1 (A), D8.1 (A), D9.1 (A), D10.1 (A), D11.1 (A), D12.1 (A), R1.1

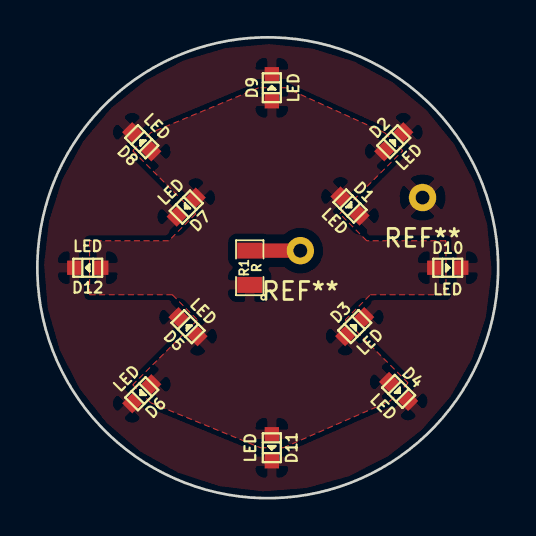
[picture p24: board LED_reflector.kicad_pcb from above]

Board: 2 copper layers, 25.6 x 25.6 mm, 13 parts (0 on the bottom side), 2 nets.

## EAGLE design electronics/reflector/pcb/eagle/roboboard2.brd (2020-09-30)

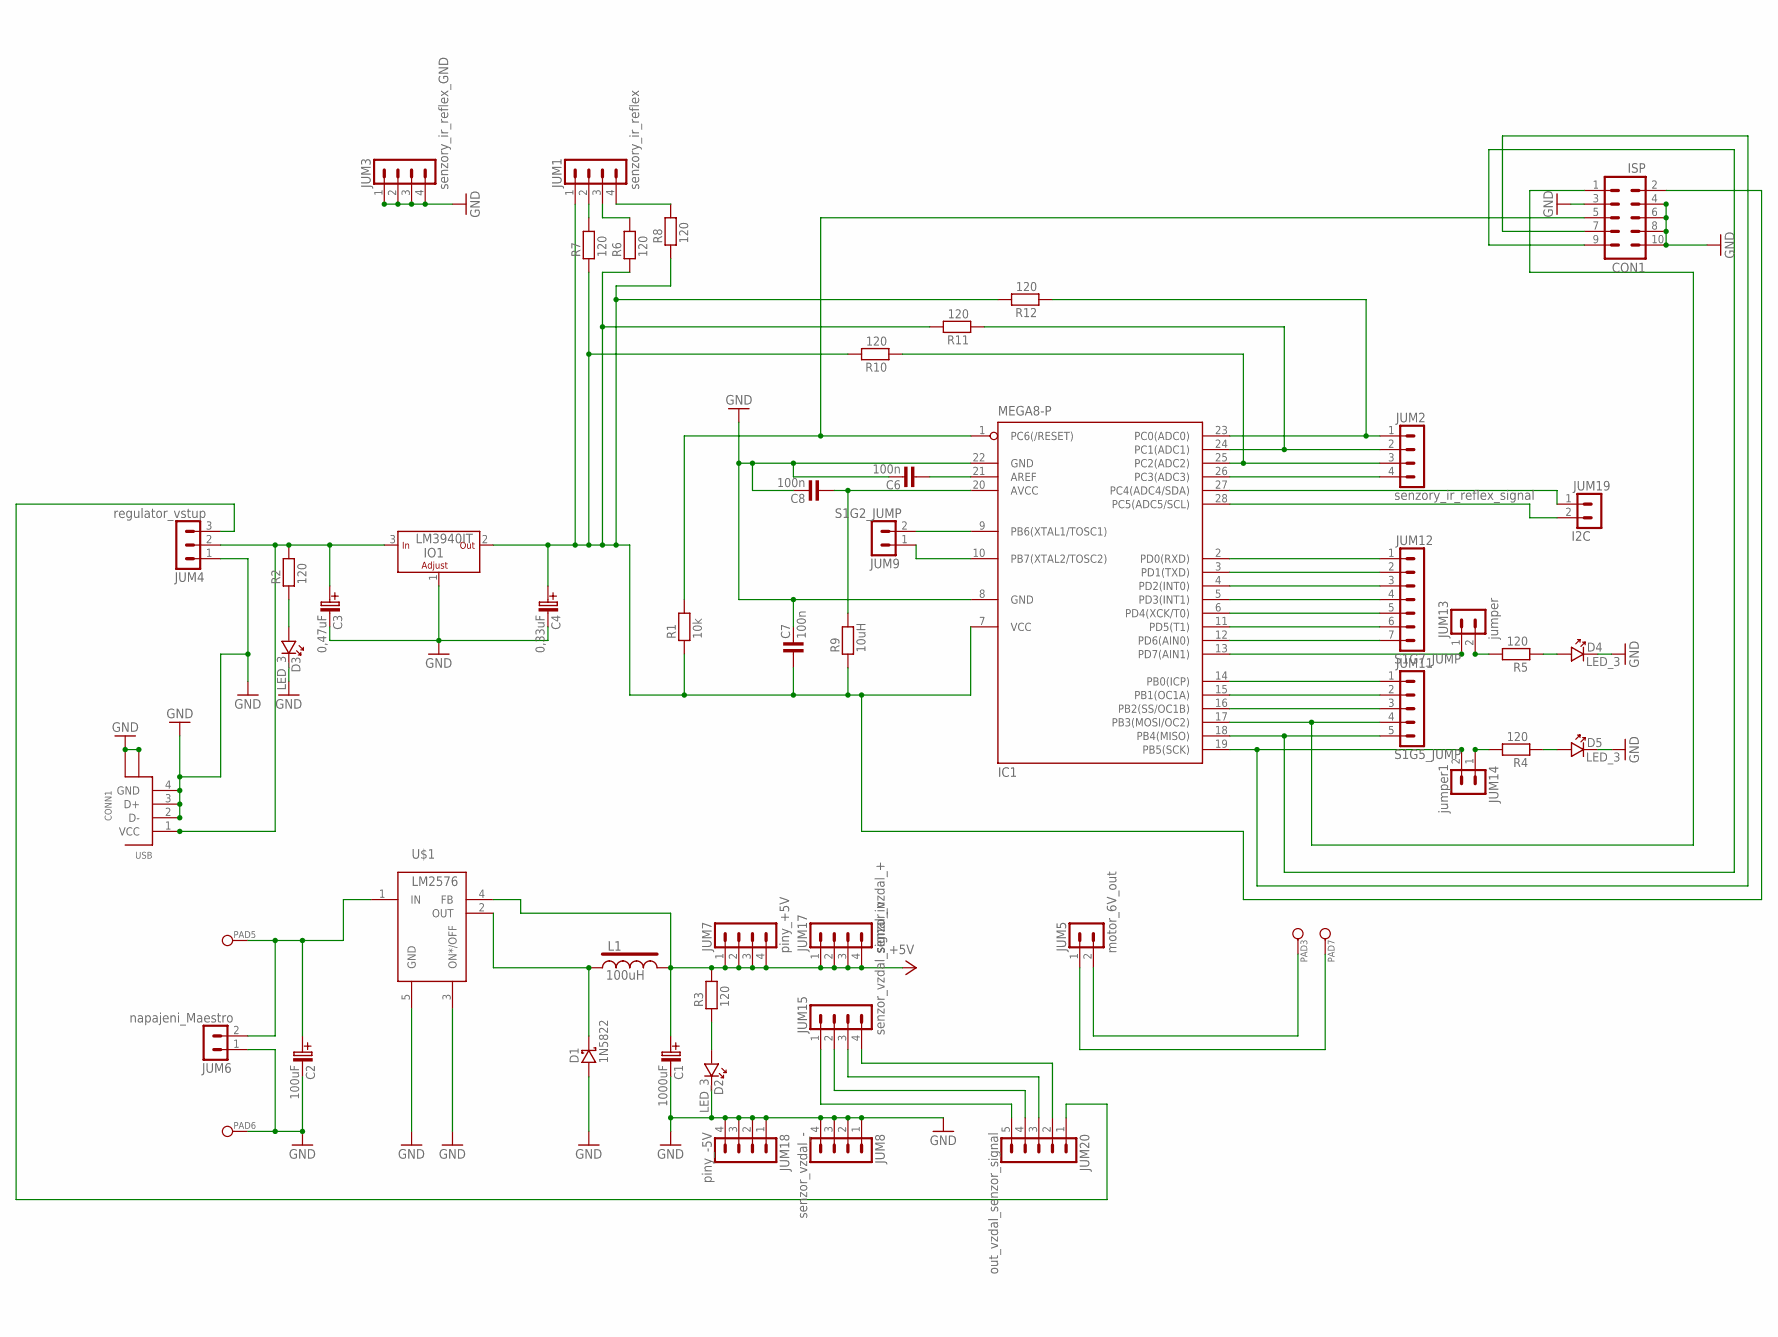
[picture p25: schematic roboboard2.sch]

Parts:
C1: 1000uF; C-EL_5
C2: 100uF; C-EL_5
C3: 0,47uF; C-EL_5
C4: 0,33uF; C-EL_3,5
C6, C7, C8: 100n; C-2,5
CON1: ISP; MLW10A
CONN1: USB; PN61729
D1: 1N5822; TO-220AC
D2, D3, D4, D5: LED_3
IC1: MEGA8-P; DIL28-3
IO1: LM3940IT; TO-220
JUM1: senzory_ir_reflex; S1G4_JUM
JUM2: senzory_ir_reflex_signal; S1G4_JUM
JUM3: senzory_ir_reflex_GND; S1G4_JUM
JUM4: regulator_vstup; S1G3_JUM
JUM5: motor_6V_out; S1G2_JUM
JUM6: napajeni_Maestro; S1G2_JUM
JUM7: piny_+5V; S1G4_JUM
JUM8: senzor_vzdal_-; S1G4_JUM
JUM9: S1G2_JUMP; S1G2_JUM
JUM11: S1G5_JUMP; S1G5_JUM
JUM12: S1G7_JUMP; S1G7_JUM
JUM13: jumper; S1G2_JUM
JUM14: jumper1; S1G2_JUM
JUM15: senzor_vzdal_signal_in; S1G4_JUM
JUM17: senzor_vzdal_+; S1G4_JUM
JUM18: piny_-5V; S1G4_JUM
JUM19: I2C; S1G2_JUM
JUM20: out_vzdal_senzor_signal; S1G5_JUM
L1: 100uH; FED_2200
PAD3: motor_6V_in; PAD_1
PAD5: 11,1V; PAD_1
PAD6: PAD_1-; PAD_1
PAD7: 6V_motor; PAD_1
R1: 10k; R-10
R2, R3, R4, R5, R6, R7, R8, R10, R11, R12: 120; R-10
R9: 10uH; R-10
U$1: LM2576

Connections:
+5V: C1.C+ (C_EL+), JUM7.1, JUM7.2, JUM7.3, JUM7.4, JUM17.1, JUM17.2, JUM17.3, JUM17.4, L1.2, R3.2, U$1.4 (FB)
GND: C1.C- (C_EL-), C2.C- (C_EL-), C3.C- (C_EL-), C4.C- (C_EL-), C6.2, C7.2, C8.2, CON1.3, CON1.4, CON1.6, CON1.8, CON1.10, CONN1.2 (D-), CONN1.3 (D+), CONN1.4 (GND), CONN1.P$1, CONN1.P$2, D1.A, D2.K, D3.K, D4.K, D5.K, IC1.8 (GND), IC1.22 (GND), IO1.1 (ADJ), JUM3.1, JUM3.2, JUM3.3, JUM3.4, JUM4.1, JUM6.1, JUM8.1, JUM8.2, JUM8.3, JUM8.4, JUM18.1, JUM18.2, JUM18.3, JUM18.4, PAD6.1, U$1.3 (ON*/OFF), U$1.5 (GND)
unnamed: D1.K, L1.1, U$1.2 (OUT)
unnamed: C6.1, IC1.21 (AREF)
unnamed: C8.1, IC1.20 (AVCC), R9.2
unnamed: CON1.5, IC1.1 (PC6(/RESET)), R1.2
unnamed: IC1.24 (PC1(ADC1)), JUM2.2, R11.1
unnamed: IC1.25 (PC2(ADC2)), JUM2.3, R10.1
unnamed: IC1.23 (PC0(ADC0)), JUM2.1, R12.1
unnamed: IC1.26 (PC3(ADC3)), JUM2.4
unnamed: IC1.27 (PC4(ADC4/SDA)), JUM19.1
unnamed: IC1.28 (PC5(ADC5/SCL)), JUM19.2
unnamed: IC1.2 (PD0(RXD)), JUM12.1
unnamed: IC1.3 (PD1(TXD)), JUM12.2
unnamed: IC1.4 (PD2(INT0)), JUM12.3
unnamed: IC1.5 (PD3(INT1)), JUM12.4
unnamed: IC1.6 (PD4(XCK/T0)), JUM12.5
unnamed: IC1.11 (PD5(T1)), JUM12.6
unnamed: IC1.12 (PD6(AIN0)), JUM12.7
unnamed: IC1.13 (PD7(AIN1)), JUM13.1
unnamed: IC1.14 (PB0(ICP)), JUM11.1
unnamed: IC1.15 (PB1(OC1A)), JUM11.2
unnamed: CON1.1, IC1.17 (PB3(MOSI/OC2)), JUM11.4
unnamed: IC1.16 (PB2(SS/OC1B)), JUM11.3
unnamed: CON1.9, IC1.18 (PB4(MISO)), JUM11.5
unnamed: CON1.7, IC1.19 (PB5(SCK)), JUM14.2
unnamed: JUM5.1, PAD7.1
unnamed: IC1.9 (PB6(XTAL1/TOSC1)), JUM9.2
unnamed: D4.A, R5.1
unnamed: JUM4.3, JUM20.1
unnamed: D3.A, R2.1
unnamed: D2.A, R3.1
unnamed: C2.C+ (C_EL+), JUM6.2, PAD5.1, U$1.1 (IN)
unnamed: JUM5.2, PAD3.1
unnamed: IC1.10 (PB7(XTAL2/TOSC2)), JUM9.1
unnamed: D5.A, R4.1
unnamed: JUM13.2, R5.2
unnamed: JUM1.2, R7.2
unnamed: JUM1.3, R6.2
unnamed: JUM1.4, R8.2
unnamed: JUM14.1, R4.2
unnamed: JUM15.1, JUM20.5
unnamed: JUM15.2, JUM20.4
unnamed: JUM15.3, JUM20.3
unnamed: JUM15.4, JUM20.2
unnamed: C4.C+ (C_EL+), C7.1, CON1.2, IC1.7 (VCC), IO1.2 (OUT), JUM1.1, R1.1, R6.1, R7.1, R8.1, R9.1, R10.2, R11.2, R12.2
VCC: C3.C+ (C_EL+), CONN1.1 (VCC), IO1.3 (IN), JUM4.2, R2.2

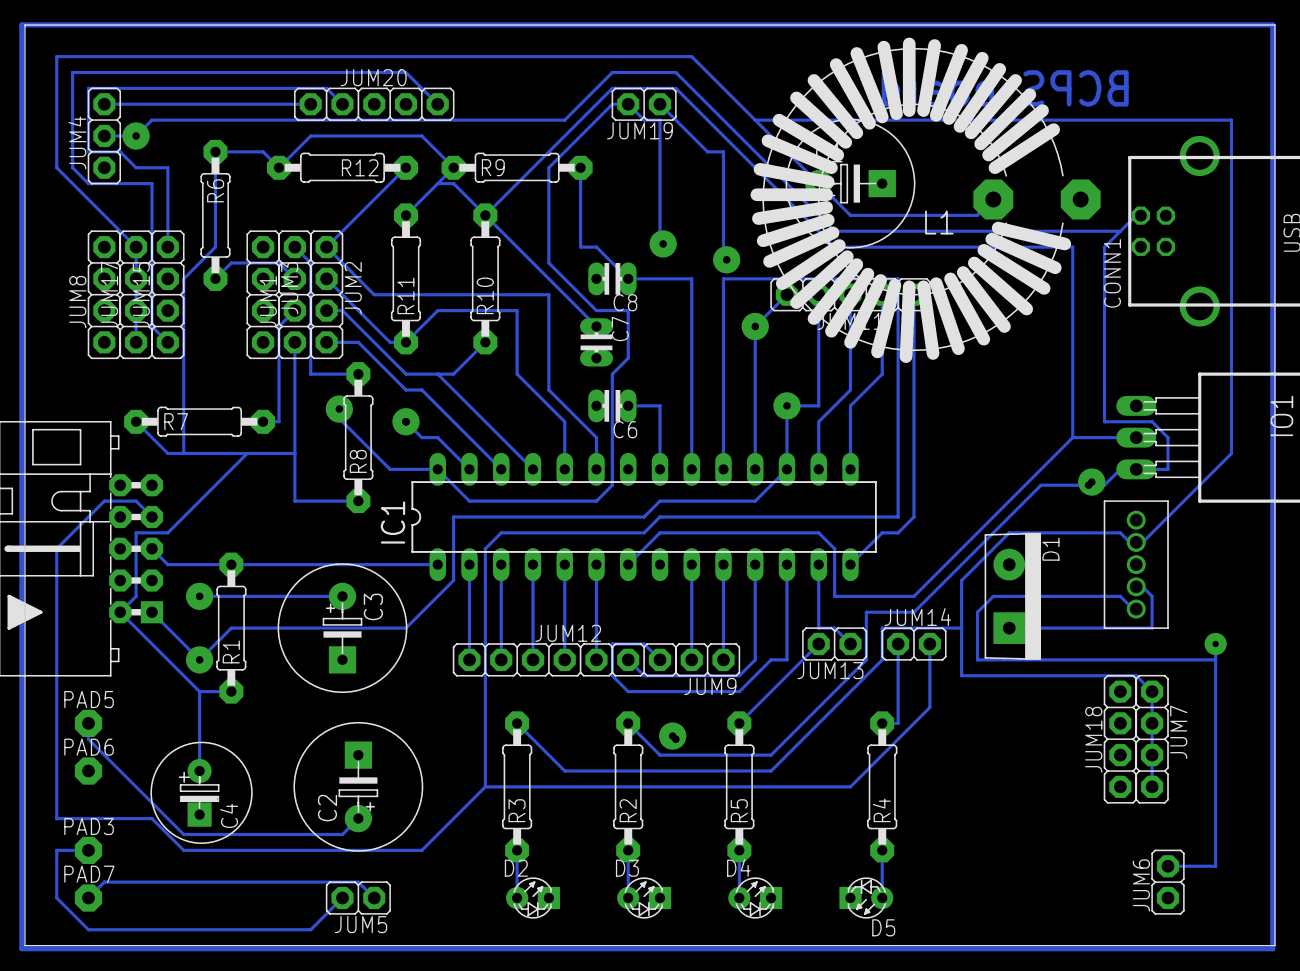
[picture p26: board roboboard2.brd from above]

Board: 2 copper layers, 100.0 x 73.6 mm, 52 parts (0 on the bottom side), 47 nets.

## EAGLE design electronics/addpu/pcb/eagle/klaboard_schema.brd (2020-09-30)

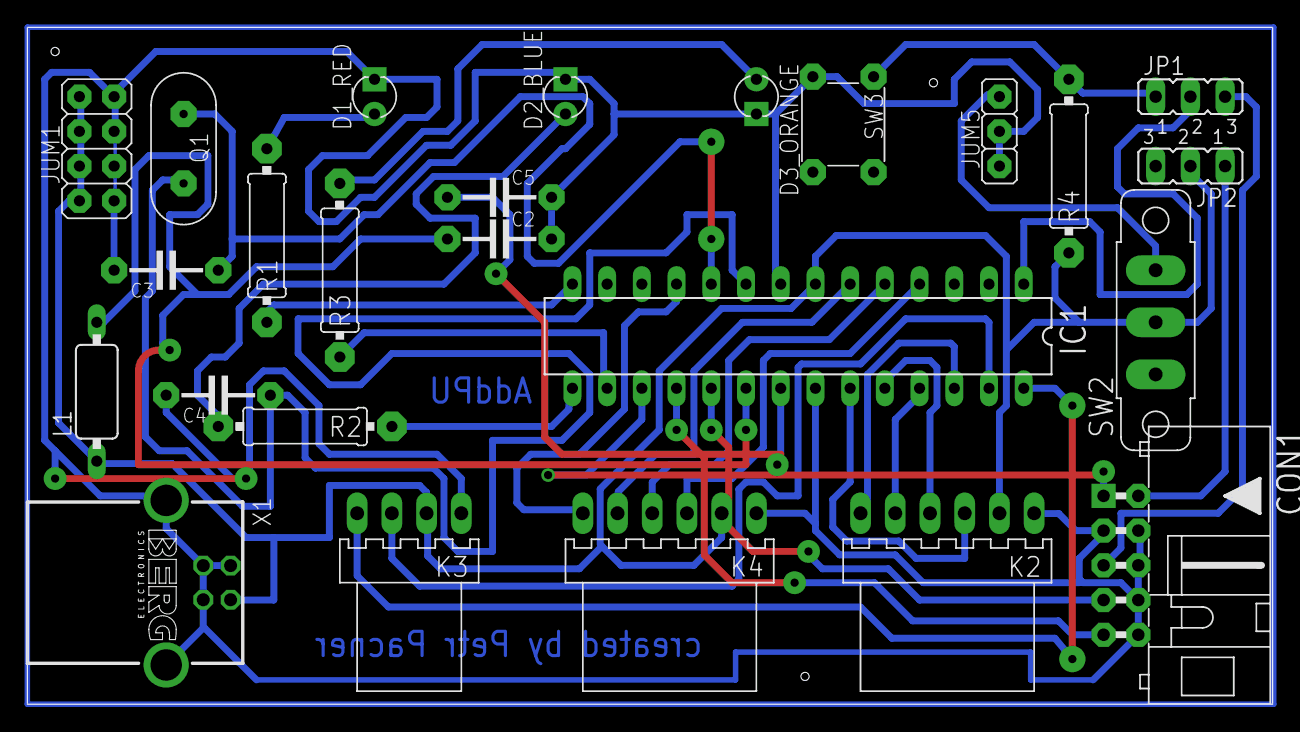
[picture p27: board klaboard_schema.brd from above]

Board: 2 copper layers, 91.1 x 49.5 mm, 25 parts (0 on the bottom side), 30 nets.

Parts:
C2, C5: 100nF; C-7,5
C3, C4: 22picoF; C-7,5
CON1: MLW10_90; MLW10A
D1_RED: ERROR; LED_3
D2_BLUE: TWI-in_progress; LED_3
D3_ORANGE: Program_ready; LED_3
IC1: MEGA8-P; DIL28-3
JP1, JP2: JP2
JUM1: S2G4_JUMP; S2G4_JUM
JUM5: S1G3_JUMP; S1G3_JUM
K2: Sensor_signal; PSH02-06W
K3: I2C; PSH02-04W
K4: Enkodery; PSH02-06W
L1: 10microH; SBC10
Q1: 16MHz; HC-49U
R1: 200; R-12,7
R2: 100; R-12,7
R3: 180; R-12,7
R4: 10k; R-12,7
SW2: P-B144
SW3: P-B1720
X1: RPi; PN61729-S

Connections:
+5V: IC1.7, JP2.2, JUM1.2_1, JUM1.2_2, JUM1.2_3, JUM1.2_4, K2.2, K3.2, K4.2, L1.1, R4.1, SW2.2, X1.1
GND: C2.2, C3.2, C4.2, C5.2, CON1.3, CON1.4, CON1.6, CON1.8, CON1.10, D1_RED.K, D2_BLUE.K, D3_ORANGE.K, IC1.8, IC1.22, JUM1.1_1, JUM1.1_2, JUM1.1_3, JUM1.1_4, JUM5.1, JUM5.2, K2.1, K3.1, K4.1, SW3.1, X1.2, X1.3, X1.4, X1.S1, X1.S2
unnamed: IC1.28, K3.4
unnamed: C2.1, IC1.20, L1.2
unnamed: IC1.4, K4.3
unnamed: IC1.5, K4.4
unnamed: IC1.6, K4.5
unnamed: IC1.11, K4.6
unnamed: C3.1, IC1.10, Q1.1
unnamed: C4.1, IC1.9, Q1.2
unnamed: C5.1, IC1.21
unnamed: IC1.14, R1.1
unnamed: IC1.27, K3.3
unnamed: CON1.1, IC1.17
unnamed: CON1.2, JP2.1
unnamed: IC1.1, JP1.2
unnamed: JUM5.3, SW2.3
unnamed: CON1.7, IC1.19
unnamed: CON1.9, IC1.18
unnamed: IC1.15, R2.1
unnamed: IC1.16, R3.1
unnamed: D3_ORANGE.A, R3.2
unnamed: D2_BLUE.A, R2.2
unnamed: D1_RED.A, R1.2
unnamed: IC1.26, K2.6
unnamed: IC1.25, K2.5
unnamed: IC1.24, K2.4
unnamed: IC1.23, K2.3
unnamed: JP1.1, R4.2, SW3.2
unnamed: CON1.5, JP1.3

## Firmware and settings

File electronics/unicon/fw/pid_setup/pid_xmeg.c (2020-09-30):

//FIXME add licence!

/* pid_xmeg.c
 * 
 * DATE:  Wed Feb 10 16:04:02 CET 2016
 * AUTHOR: PETR PACNER
 * Rev: 0.1
 *
 * DESCRIPTION:
 * THis program should be use to generate and setup curve of pid equation on the ATxmega
 *
 * WARNING
 * if you want to edit this code, make sure you didn't write an unsupported symbol (maybe a space)
 * After compile you get ERROR stray \'302\
 *
 * NOTES
 * NULL diameter sabertooth (730 - 755)
 * motor0 - PD regulator -> P=1;I=0;D=16
 * motor1 - PD regulator -> P=1/4;I=0;D=10
*/

#define F_CPU 32000000UL //Frequency 32MHz
#define Prescaler TC_CLKSEL_DIV64_gc //prescaler 64

//period equaton: fclk/(prescaler*frq-1)
#define PWM_PER (32000000/(3150)) //signal for motors [50Hz]
#define MIDPOSITION 745 // 1.5ms signal middle position for motors [width = MIDPOSITION +- 347]
#define MIDUP 755
#define MIDDOWN 730


/*LIBRARIES & HEADERS*/
#include <avr/io.h> //MACROS
#include <avr/interrupt.h> //INTERRUPT settings
#include <util/delay.h> //DELAY_MS()
#include <stdio.h>

/*GLOBAL VARIABLES*/
volatile int enk_val [] ={0, 0}; //encoders current value [enk0, enk1]
volatile int enk_val_ls [] ={0, 0}; //encoders last value
volatile int curr_spd [] ={0, 0}; //current speed array
volatile int last_spd [] ={0, 0}; //4 ticks / 20ms
volatile int req_spd [] ={0, 0}; //required speed, this variable change speed of robot
volatile int e_sum[] ={0, 0}; //integration part of regulator
volatile uint8_t front[] ={0, 0}; //array for front proximity sensor output values
volatile int e[] ={0, 0}; //speed difference
volatile int e_der[] ={0, 0};
volatile int e_enk[] ={0, 0};
uint8_t mode =0;
volatile uint8_t pulse[] ={0, 0};

static volatile int16_t pGain, iGain, dGain;
//static const int8_t dGain = 67;//134
static volatile int16_t iState[] ={0, 0};
static volatile int16_t dState[] ={0, 0};
static const int16_t iMax = 400;
static const int16_t iMin = -400;
volatile int16_t position =0;
volatile int16_t pos[] ={0, 0};

/*POINTERS TO REGISTERS*/
volatile uint8_t *twi_slv = (volatile uint8_t *) &TWIC_SLAVE_STATUS;
volatile uint8_t *twi_data = (volatile uint8_t *) &TWIC_SLAVE_DATA;
volatile uint16_t *motor0 = (volatile uint16_t *) &TCD1.CCA; //motor0
volatile uint16_t *motor1 = (volatile uint16_t *) &TCE0.CCD; //motor1
volatile uint8_t *enk0 = (volatile uint8_t *) &PORTD_IN; //PORTD STATUS
volatile uint8_t *enk1 = (volatile uint8_t *) &PORTE_IN; //PORTE STATUS
volatile uint8_t *modept = &mode;

/*INTERN OSCILATOR*/
//32MHz
void mcu_clk32_init(){
  OSC.CTRL |= OSC_RC32MEN_bm; //set 32MHz oscilator
  while(!(OSC.STATUS & OSC_RC32MRDY_bm)); //wait for oscilator to be prepared
  CCP = CCP_IOREG_gc;
  CLK.CTRL = (CLK.CTRL & ~CLK_SCLKSEL_gm) | CLK_SCLKSEL_RC32M_gc;
}

void led_init(){
  PORTA.DIRSET = (1<<PIN4) | (1<<PIN5) | (1<<PIN6); //initialize LEDs (A4; A5; A6)
}

/*TWI_INTERFACE*/
void twi_init_slv(){
  TWIC_SLAVE_ADDR = 0x65; //slave address 0x18
  TWIC_SLAVE_CTRLA = TWI_SLAVE_ENABLE_bm; //enable twi slave device
}

void rpi_com(){
  uint8_t buffer[] ={0, 0};
  while(!(*twi_slv & TWI_SLAVE_APIF_bm)); //wait for master action
  //write
  if((*twi_slv & TWI_SLAVE_DIR_bm) ==0){
    cli();
    TWIC_SLAVE_CTRLB = TWI_SLAVE_CMD_RESPONSE_gc; //send back address
    //waiting for 7bytes
    for(int i =0; i<4; ++i){
      cli();
      while(!(*twi_slv & TWI_SLAVE_DIF_bm));
      buffer[0] = TWIC_SLAVE_DATA; //save received value
      TWIC_SLAVE_CTRLB = TWI_SLAVE_CMD_RESPONSE_gc; //send data
      //if(buffer[0] !=0) PORTA.OUTSET = (1<<PIN4);

      while(!(*twi_slv & TWI_SLAVE_DIF_bm));
      buffer[1] = TWIC_SLAVE_DATA; //save received value
      //if(buffer[1] ==220) PORTA.OUTSET = (1<<PIN4);
      if(i != 3)
        TWIC_SLAVE_CTRLB = TWI_SLAVE_CMD_RESPONSE_gc; //send data
      else
        TWIC_SLAVE_CTRLB = TWI_SLAVE_CMD_COMPTRANS_gc;
      //sei();
      
      switch(i){
      case 0:
          pGain =(buffer[0] <<8)|buffer[1];
          //PORTA.OUTSET = (1<<PIN4);
      case 1:
          iGain =(buffer[0] <<8)|buffer[1];
      case 2:
          dGain =(buffer[0] <<8)|buffer[1];
      case 3:
          position =(buffer[0] <<8)|buffer[1];
      }
    }
    sei();
  }
  //read
  else if((*twi_slv & TWI_SLAVE_DIR_bm) !=0){ //do you want to transmitt more bytes   
    cli();
    TWIC_SLAVE_CTRLB = TWI_SLAVE_CMD_RESPONSE_gc; //ACK after address recieved
    while(!(*twi_slv & TWI_SLAVE_DIF_bm));
    *twi_data = pulse[0];
    TWIC_SLAVE_CTRLB = TWI_SLAVE_CMD_RESPONSE_gc; //send data
    while(!(*twi_slv & TWI_SLAVE_DIF_bm));
    *twi_data = pulse[1];
    TWIC_SLAVE_CTRLB = TWI_SLAVE_CMD_RESPONSE_gc; //send data
    while(!(*twi_slv & TWI_SLAVE_DIF_bm));
    TWIC_SLAVE_CTRLB = TWI_SLAVE_CMD_COMPTRANS_gc | 0x04; //send NACK
    sei();
  }
}

//split number into two bytes and return the byte on submited position
void split_num(volatile int num, volatile uint8_t array[2])
{
  //uint16_t num = numpt;
  array[0] = (num >>8) & 0xff;
  array[1] = 0xff & num;
}

uint16_t pid0(int16_t r){
  volatile int16_t y = enk_val[0];
  volatile int32_t u;
  volatile int32_t pTerm;
  volatile int32_t dTerm;
  volatile int32_t iTerm;
  volatile int32_t e = r - y;

  iState[0] += e; 
  if (iState[0] > iMax)
    iState[0] = iMax;
  else if (iState[0] < iMin)
    iState[0] = iMin;

  pTerm = e;
  iTerm = 0;//(iGain*iState[0]);
  dTerm = (16*(y - dState[0]));
  dState[0] = y;

  u = pTerm +iTerm -dTerm;
  //split_num(u, pulse); 
  
  if(u >0)//move null point up?
    u += MIDUP;
  else if(u ==0)
    u += MIDPOSITION;
  else if(u <0)//move null point down
    u += MIDDOWN;

  if(u > 1080)//MAX supported motor pulse
  //if(u > 804)
      u = 1080;
  //else if(u < 581)
  else if (u < 406)//MIN supported motor pulse
      u = 406;
  return (uint16_t) u;
}

uint16_t pid1(int16_t r){
  volatile int16_t y = enk_val[1];
  volatile int32_t u;
  volatile int32_t pTerm;
  volatile int32_t dTerm;
  volatile int32_t iTerm;
  volatile int32_t e = r - y;

  iState[1] += e; 
  if (iState[1] > iMax)
    iState[1] = iMax;
  else if (iState[1] < iMin)
    iState[1] = iMin;

  pTerm = e/4;
  iTerm = 0; //(iGain*iState[1]);
  dTerm = (10*(y - dState[1]));
  dState[1] = y;

  u = pTerm +iTerm -dTerm;
  //split_num(u, pulse); 
  
  if(u >0)//move null point up?
    u += MIDUP;
  else if(u ==0)
    u += MIDPOSITION;
  else if(u <0)//move null point down
    u += MIDDOWN;

  if(u > 1080)//MAX supported motor pulse
  //if(u > 804)
      u = 1080;
  //else if(u < 581)
  else if (u < 406)//MIN supported motor pulse
      u = 406;
  return (uint16_t) u;
}

/*SINGLE_SLOPE_GENERATION*/
//motor0 - D4; motor1 - E3
//TIMER1 PORTD
void motor0_init(){
  PORTD.DIR |= (1<<PIN4); //set pin as output
  TCD1.CTRLB = TC_WGMODE_SS_gc|TC1_CCAEN_bm; //set single slope mode 
  //TCD1.INTCTRLA = TC_OVFINTLVL_HI_gc;
  TCD1.PER = PWM_PER; //period
  TCD1.CTRLA = Prescaler; //prescaler
  *motor0 = MIDPOSITION;
}

//TIMER0 PORTE
void motor1_init(){
  PORTE.DIR |= (1<<PIN3); //set pin as output
  TCE0.CTRLB = TC_WGMODE_SS_gc|TC0_CCDEN_bm; //set single slope mode
  TCE0.PER = PWM_PER; //period
  TCE0.CTRLA = Prescaler; //prescaler
  *motor1 = MIDPOSITION; //set motor in middle position
  /*SET PWM FOR MOTORS*/
  //pulswidth between (396 - 1090)
  //null point for sabertooth == 743
  //increase value --> revers move
  //decrease value --> forward move
}

void motor_ctrl(){
  TCD0.CTRLB = TC_WGMODE_SS_gc; //set single slope mode 
  TCD0.INTCTRLA = TC_OVFINTLVL_HI_gc;
  TCD0.PER = 499; //1kHz
  TCD0.CTRLA = Prescaler; //prescaler TC_CLKSEL_DIV8_gc;
}

ISR(TCD0_OVF_vect){
  if(*modept ==1){
    *motor1 = pid1(pos[1]);
    *motor0 = pid0(pos[0]);
  }
  //split_num(enk_val[0], pulse);
}

/*MODE INTERRUPT*/
//interrupt - C3
void mode_init(){
  PORTC.INT0MASK = (1<<PIN3);
  PORTC.PIN3CTRL = PORT_ISC_FALLING_gc;
  PORTC.INTCTRL |= PORT_INT0LVL_HI_gc;
  PMIC.CTRL |= PMIC_HILVLEN_bm |PMIC_MEDLVLEN_bm|PMIC_LOLVLEN_bm;
}
//swich mode
ISR(PORTC_INT0_vect){
  if(*modept == 1) 
    *modept =0;
  else
    *modept +=1;
}  

/*ENCODER INTERRUPTS*/
void enk0_init(){
  PORTD.INT0MASK = (1<<PIN2);
  PORTD.PIN2CTRL = PORT_ISC_BOTHEDGES_gc;
  PORTD.INTCTRL |= PORT_INT0LVL_HI_gc;
  PMIC.CTRL |= PMIC_HILVLEN_bm |PMIC_MEDLVLEN_bm|PMIC_LOLVLEN_bm;
}

ISR(PORTD_INT0_vect){
    //current statement of PIN3
    if((*enk0 & PIN2_bm) ==0){
      if((*enk0 & PIN3_bm) ==0){
        cli();
        enk_val[0] -=1;
        sei();
      }
      else{
        cli();
        enk_val[0] +=1;
        sei();
      }
    }
    else{
      if((*enk0 & PIN3_bm) ==0){
        cli();
        enk_val[0] +=1;
        sei();
      }
      else{
        cli();
        enk_val[0] -=1;
        sei();
      }
   }
    /*
   //overflow protection
   if(enk_val[0] ==32500 || enk_val[0] ==-32500){
     enk_val[0] =enk_val[0]-enk_val_ls[0];
     enk_val_ls[0] =0;
   }
   */
}

void enk1_init(){
  PORTE.INT0MASK = (1<<PIN2);
  PORTE.PIN2CTRL = PORT_ISC_BOTHEDGES_gc;
  PORTE.INTCTRL |= PORT_INT0LVL_HI_gc;
  PMIC.CTRL |= PMIC_HILVLEN_bm |PMIC_MEDLVLEN_bm|PMIC_LOLVLEN_bm;
}

ISR(PORTE_INT0_vect){
  //PIN4
  if((*enk1 & PIN2_bm) ==0){
    if((*enk1 & PIN4_bm) ==0){
      cli();
      enk_val[1] +=1;
      sei();
    }
    else{
      cli();
      enk_val[1] -=1;
      sei();
    }
  }
  else{
    if((*enk1 & PIN4_bm) ==0){
      cli();
      enk_val[1] -=1;
      sei();
    }
    else{
      cli();
      enk_val[1] +=1;
      sei();
    }
  }
}

void turn(int16_t tics){
  for(int i =0; i<=tics; ++i){
    pos[0] +=1;
    pos[1] -=1;
    _delay_ms(2);
  }
}

int main(){ 
  /*LOCAL VARIABLES*/

  /*INITIALIZATION*/
  mcu_clk32_init(); //initilize 32MHz intern oscilator
  led_init(); //initialize control LED connected to ATxmega64
  //twi_init_slv(); //slave device initialization

  /*INTERRUPTS_INITIALIZE*/
  mode_init(); //initialize mode button interrupt
  enk0_init(); // -||- encoder0 (motor0)
  enk1_init(); // -||- encoder1 (motor1)

  /*TIMERS_INITIALIZE*/
  motor0_init();
  motor1_init();
  motor_ctrl();

  sei(); //TURN ON ALL INTERRUPTS
  
  while(1){
    switch (*modept){
      case 0:
        PORTA.OUTCLR = (1<<PIN5) | (1<<PIN6);
        while(*modept ==0);

      case 1:
        PORTA.OUTCLR = (1<<PIN5) | (1<<PIN6);
        PORTA.OUTSET = (1<<PIN6);
        turn(1000);

        while(*modept ==1){
          if(enk_val[0] ==1000)
            PORTA.OUTSET = (1<<PIN4);
          else
            PORTA.OUTCLR = (1<<PIN4);

          //rpi_com();
        }
    }
  }
  return 0;
}

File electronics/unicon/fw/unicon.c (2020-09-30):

//FIXME add licence!

/* unicon.c
 * 
 * DATE:  Wed Feb 10 16:04:02 CET 2016
 * AUTHOR: PETR PACNER
 * Rev: 0.1
 *
 * DESCRIPTION:
 * 
 * The main purpose of this program is controlling robot movemets board.
 * Is't upload in flash memory of atxmega64, which is the brain of this board.
 * This program contains different modes for distinctive robot behavior.
 *
 * WARNING
 * if you want to edit this code, make sure you didn't write an unsupported symbol (maybe a space)
 * After compile you get ERROR stray \'302\
*/

#define F_CPU 32000000UL //Frequency 32MHz
#define Prescaler TC_CLKSEL_DIV64_gc //prescaler 8

//period equaton: fclk/(prescaler*frq-1)
#define PWM_PER (32000000/(3150)) //signal for motors [50Hz]
#define MIDPOSITION 745 // 1.5ms signal middle position
#define ROTATE 660 //number of pulse to turn 90degree (680-passage)
#define SPEED 5 //speed of arm moves
#define SPDMOV 10
#define ERROR 5
#define MEASUREMENT_N 20 //number of measure samples
#define STRADDR 36 //start addres for proximity sensors 
#define ANGLE90 1450

//I2C device addresses
#define RIGHT 0x28
#define FRONT0 0x27
#define FRONT1 0x26
#define LEFT 0x25
#define BACK 0x24
#define COMPASS 0x1e
#define LED_DVR 0x60

//NATIVE SERVO POSITIONS
#define SERVO0 635
#define SERVO1 1235
#define SERVO2 1195
#define SERVO3 560
#define SERVO4 750
#define SERVO5 520//780

/*LIBRARIES & HEADERS*/
#include <avr/io.h> //MACROS
#include <avr/interrupt.h> //INTERRUPT settings
#include <util/delay.h> //DELAY_MS()
#include <stdio.h>

/*GLOBAL VARIABLES & ARRAYS*/
volatile int16_t enk_val [] ={0, 0}; //encoders current value [enk0, enk1]
volatile int16_t enk_val_ls [] ={0, 0}; //encoders last value
volatile int16_t curr_spd [] ={0, 0}; //current speed array
volatile int16_t last_spd [] ={0, 0}; //4 ticks / 20ms
volatile int16_t req_spd [] ={0, 0}; //required speed, this variable change speed of robot
volatile int16_t e_sum[] ={0, 0}; //integral state for PID 
volatile uint16_t motors[] ={0, 0};
volatile int16_t position[] ={0, 0};
volatile int16_t dState[] ={0, 0};
uint8_t mode =0;
uint8_t mov =0; //indicate operation in the robot movement (set exact position or set speed of motors)

//CONTROL BYTES
uint8_t refl[] ={0x06, 0x15}; //register and address of reflector
uint8_t blue0[] ={0x06, 0x05}; //register and address of blue led LED_driver
uint8_t blue1[] ={0x06, 0x11}; //register and address of second blue led
uint8_t all[] ={0x06, 0x01}; //turn on all LEDs

/*POINTERS TO REGISTERS*/
volatile uint8_t *twi_stat = (volatile uint8_t *) &TWID_MASTER_STATUS;
volatile uint8_t *twi_data = (volatile uint8_t *) &TWIC_SLAVE_DATA;

//ROBOTIC_ARM
volatile uint16_t *servo0 = (volatile uint16_t *) &TCF1.CCA; //robotic arm motion
volatile uint16_t *servo1 = (volatile uint16_t *) &TCF1.CCB; //main part1(biggest)
volatile uint16_t *servo2 = (volatile uint16_t *) &TCF0.CCB; //main part2(middle)
volatile uint16_t *servo3 = (volatile uint16_t *) &TCF0.CCD; //main part3(smallest)
volatile uint16_t *servo4 = (volatile uint16_t *) &TCF0.CCC; //arm jawes motion
volatile uint16_t *servo5 = (volatile uint16_t *) &TCF0.CCA; //arm jawes
volatile uint16_t *motor0 = (volatile uint16_t *) &TCD1.CCA; //motor0
volatile uint16_t *motor1 = (volatile uint16_t *) &TCE0.CCD; //motor1
volatile uint8_t *enk0 = (volatile uint8_t *) &PORTD_IN; //PORTD STATUS
volatile uint8_t *enk1 = (volatile uint8_t *) &PORTE_IN; //PORTE STATUS
volatile uint8_t *modept = &mode; //pointer to mode variable
volatile uint8_t *movpt = &mov; //pointer to mov variable

/*INTERN OSCILATOR*/
//2MHz
void mcu_clk2_init(){
  OSC.CTRL |= OSC_RC2MEN_bm; //set 2MHz oscilator
  while(!(OSC.STATUS & OSC_RC2MRDY_bm)); //wait for oscilator
  CCP = CCP_IOREG_gc;
  CLK.CTRL = (CLK.CTRL & ~CLK_SCLKSEL_gm) | CLK_SCLKSEL_RC32M_gc; //activete oscilator
}

//32MHz
void mcu_clk32_init(){
  OSC.CTRL |= OSC_RC32MEN_bm; //set 32MHz oscilator
  while(!(OSC.STATUS & OSC_RC32MRDY_bm)); //wait for oscilator to be prepared
  CCP = CCP_IOREG_gc;
  CLK.CTRL = (CLK.CTRL & ~CLK_SCLKSEL_gm) | CLK_SCLKSEL_RC32M_gc;
}

/*TWI_INTERFACE*/
void twi_init(){
  PORTD.PIN0CTRL = PORT_OPC_WIREDANDPULL_gc;
  PORTD.PIN1CTRL = PORT_OPC_WIREDANDPULL_gc;
  TWID_MASTER_BAUD = 0x28;//0x28; //355kHz //0x90; //106kHz
  TWID_MASTER_CTRLA = TWI_MASTER_ENABLE_bm ; // Enable TWI interface
  //TWID_MASTER_CTRLB = TWI_MASTER_SMEN_bm | TWI_MASTER_QCEN_bm;
  TWID_MASTER_STATUS = TWI_MASTER_BUSSTATE_IDLE_gc;  //set bus state to IDLE mode
  _delay_ms(5);
}

void led_init(){
  PORTA.DIRSET = (1<<PIN4) | (1<<PIN5) | (1<<PIN6); //initialize LEDs (A4; A5; A6)
}

void portH_init(){
  PORTH.DIRSET = (1<<PIN0) | (1<<PIN1) | (1<<PIN2) | (1<<PIN3) | (1<<PIN4) | (1<<PIN5); //initialize port for turn on/off sensors
  //set pull-ups on these pins

  PORTH.PIN0CTRL |= PORT_OPC_WIREDANDPULL_gc;
  PORTH.PIN1CTRL |= PORT_OPC_WIREDANDPULL_gc;
  PORTH.PIN2CTRL |= PORT_OPC_WIREDANDPULL_gc;
  PORTH.PIN3CTRL |= PORT_OPC_WIREDANDPULL_gc;
  PORTH.PIN4CTRL |= PORT_OPC_WIREDANDPULL_gc;
  PORTH.PIN5CTRL |= PORT_OPC_WIREDANDPULL_gc;
  /*
   * PIN0 - sensor BACK
   * PIN1 - sensor LEFT
   * PIN2 - sensor FRONT1
   * PIN3 - compass speed_up function
   * PIN4 - sensor FRONT0 (from the right side)
   * PIN5 - sensor RIGHT
  */
}

uint8_t dev_check(uint8_t addr){
  TWID_MASTER_ADDR = (addr <<1);
  while(!(*twi_stat & TWI_MASTER_WIF_bm)); //wait for write flag is set?
  if((*twi_stat & TWI_MASTER_RXACK_bm) == TWI_MASTER_RXACK_bm){
    TWID_MASTER_CTRLC = 0x03;
    return 1;
  }
  else {
    TWID_MASTER_CTRLC = 0x03;
    return 0;
  }
}

//write number 
//if the transfer go wrong - return number is not equal to variable num
uint8_t twi_write(uint8_t device, uint8_t buff[3], uint8_t num){
  uint8_t i = 0;
  TWID_MASTER_ADDR = (device <<1);

  for(; i<num;){
    while(!(*twi_stat & TWI_MASTER_WIF_bm)); //wait for write flag is set?
    if((*twi_stat & TWI_MASTER_RXACK_bm) == TWI_MASTER_RXACK_bm) return i;
    else if((*twi_stat & TWI_MASTER_RXACK_bm) == 0){
      TWID_MASTER_DATA = buff[i];
      ++i;
      //while(!(*twi_stat & TWI_MASTER_WIF_bm));
    }
    else{
      while(!(*twi_stat & TWI_MASTER_BUSSTATE_IDLE_gc)); //wait for TWI IDLE statement
      i = 0; //set variable i to NULL 
      TWID_MASTER_ADDR = (device <<1); //send address again
    }
  }
  while(!(*twi_stat & TWI_MASTER_WIF_bm)); //wait for write flag is set?
  TWID_MASTER_CTRLC = 0x03;
  //TWID_MASTER_STATUS = TWI_MASTER_BUSSTATE_IDLE_gc;  //set bus state to IDLE mode

  return i;
}
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

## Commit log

2020-02-05 added CAD model from inventor 2013
    [10mm-komatex-profil-packa(1x).dxf, 10mm-komatex-profil-stojan(2x).dxf, 3mm-komatex-desticka_na_lozisko(8x).dxf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]
2020-02-05 added reflector pcb design
    [LED_reflector.kicad_pcb, LED_reflector.sch]
2020-03-22 new submodules sensors
2020-09-30 Raw files from original project Robot Claire
    [LED_reflector.kicad_pcb, LED_reflector.sch, ROBarm.kicad_pcb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]
2020-09-30 updated module sensors

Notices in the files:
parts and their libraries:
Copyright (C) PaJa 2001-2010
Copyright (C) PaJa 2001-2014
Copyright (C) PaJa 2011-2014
